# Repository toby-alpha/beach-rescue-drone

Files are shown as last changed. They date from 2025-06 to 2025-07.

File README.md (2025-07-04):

# Beach Rescue Drone & Dock





I designed (and will produce) a 7" drone capable of carrying a moderate payload that is a concept for a solution that would  assist in crucial life saving operations.

### Why did I design this?
 
Well... a drone is pretty cool, and my interests as soon as a saw this program definitely came to that straight away. Yet, I wanted to do something more meaningful than just a racing drone, something that could develop as unique, in a needing area. This really sparked my passion, and I feel like I was able to learn alot, while allowing my skills to thrive.

### What next?

Once all the parts arrive, there will be alot of assembly, and wiring to do. I'll be working off the Ardupilot firmware, so when I'm able to, I'll start adding that to the GitHub as well.

I'd love to answer any questions you have about this!

The STEP file contains all the CAD, it is uploaded in a ZIP file. Let me know if there are any errors with the conversions.

### PCB



### Wiring Diagram

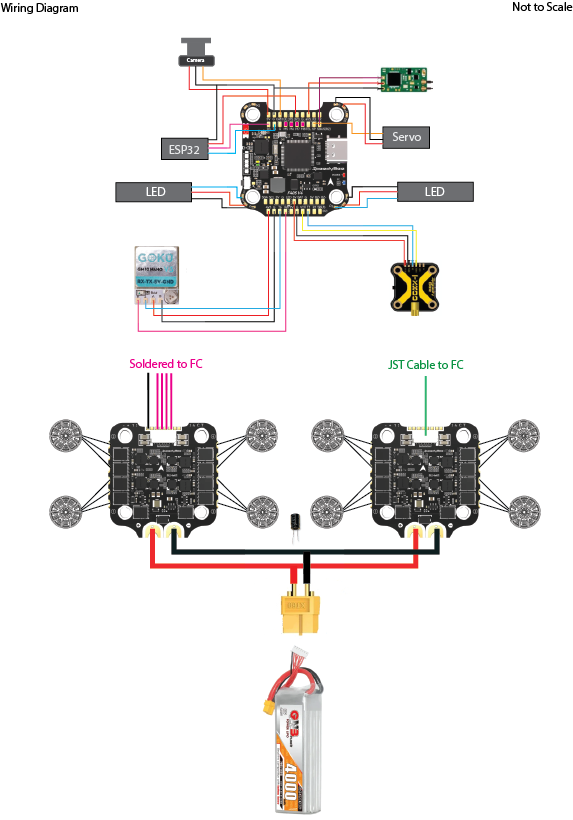
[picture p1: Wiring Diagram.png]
Wiring Diagram.png


### BOM

|Item |Cost (AUD)|Cost (USD)|Source |Link |
|---|---|---|---|---|
|2207 Motors x4 |0 |0 |Owned |N/A |
|Speedybee F405 FC |0 |0 |Owned |N/A |
|Speedybee 55A ESC |0 |0 |Owned |N/A |
|Reciever Module |0 |0 |Owned |N/A |
| | | | | |
|Speedybee 55A ESC |60 |39 |Aliexpress| |
|2207 Motors x4 |57 |37.05 |Aliexpress|https://vi.aliexpress.com/item/1005006356256645.html |
|VTX |40 |26 |Aliexpress|https://vi.aliexpress.com/item/1005006776832075.html |
|FPV Camera |38 |24.7 |Aliexpress|https://vi.aliexpress.com/item/1005009066346111.html |
|Servo and Parts |40 |26 |Aliexpress|https://vi.aliexpress.com/item/1005008716284050.html |
|ESP32 C3 |12 |7.8 |Aliexpress|https://vi.aliexpress.com/item/1005008813495235.html |
|7" Props |8 |5.2 |Aliexpress|https://vi.aliexpress.com/item/1005008250427353.html |
|Misc (bolts, standoffs)|25 |16.25 |Aliexpress|Misc. |
| | | | | |
|Aluminium Arms |150 |97.5 |Alibaba |PDF Quote (Provide upon individual request) |
|Carbon Fibre |120 |78 |Alibaba |PDF Quote (Provide upon individual request) |
|Middle Block |78 |50.7 |Alibaba |PDF Quote (Provide upon individual request) |
|Transmitter PCB |5 |3.25 |JLCPCB |PDF Quote (Provide upon individual request) |
| | | | | |
|Battery |119 |77.35 |PhaserFPV |https://phaserfpv.com.au/collections/6s-batteries/products/gaoneng-gnb-lihv-6s-228v-4000mah-70c-lipo-battery-xt60-dg|
| | | | | 
|Total |752 |488.8 | | |

## Part 2 



### Wiring Diagram


### BOM

|Item |Cost (AUD)|Cost (USD) |Source |Link |
|---|---|---|---|---|
|White PETG (14kg) |238 |154 |Siddament |https://siddament.com.au/products/white-petg-1-75mm-1kg |
|Black PETG (3kg) |48 |31.2 |Siddament |https://siddament.com.au/products/black-tpu-1-75mm-1kg |
|Linear Actuators x2 |160 |104 |Aliexpress |https://vi.aliexpress.com/item/1005006477151440.html |
|Breaker |9 |5.85 |Aliexpress |thttps://vi.aliexpress.com/item/1005006273365319.html |
|Control Board |7 |4.55 |Aliexpress |https://vi.aliexpress.com/item/1005004227086403.html |
|Control Panel |11 |7.15 |Aliexpress |https://vi.aliexpress.com/item/1005004227086403.html |
|Battery |29 |18.85 |Jaycar |https://www.jaycar.com.au/12v-6-5ah-sla-battery/p/SB2485 |
|Bearings |20 |13 |Aliexpress |https://vi.aliexpress.com/item/1005006822613982.html |
|Misc Hardware |40 |26 |Misc (Aliexpress)| |
|Total |535 |347.75 | | |

This dock is the second part of this project, and aims to serve as a succinct housing to complete it, overall completing the design goal set out at the start of the project.

Filament costs are tentative, yet on the lower side. Each piece takes roughly 1kg, and there will be 9. This doesn't account of support, or failures.

### Why I designed this?

After seeing the sucsess I had with the drone, I really wanted to nail in on the concept that I had created. The drone was great, but it needed a place to be stored. Thus, I was inspired to come up with this elegant solution. This makes my prototype become 1 step closer to a viable product, that'd be able to serve in a life saving capacity.

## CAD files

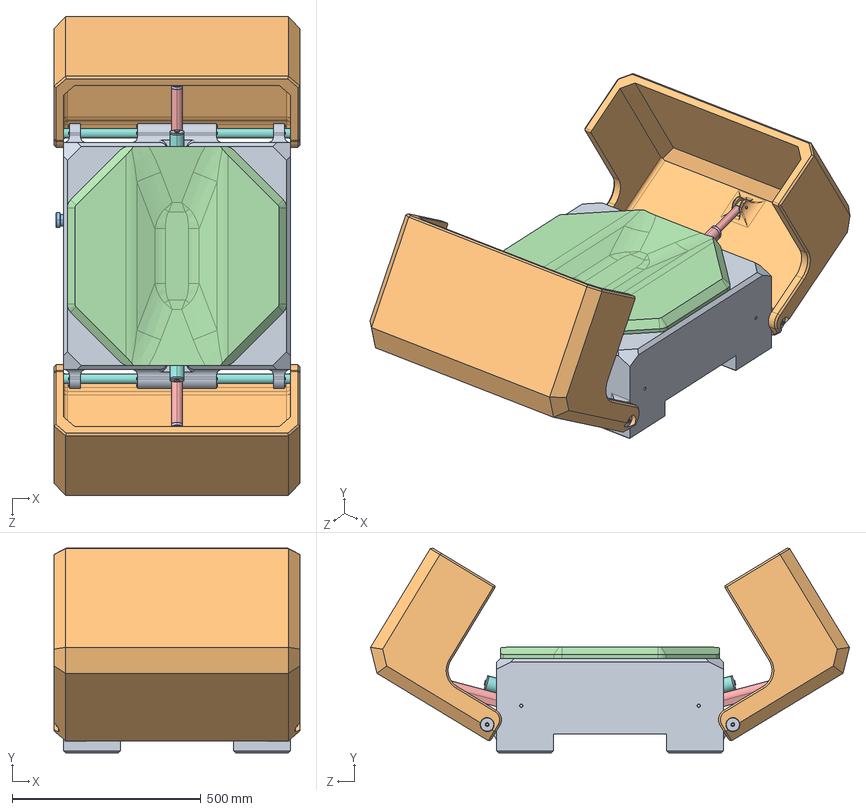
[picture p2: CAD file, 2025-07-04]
Part 2 - Dock/Dock Assembly.STEP
650.0 x 542.1 x 1267.4 mm
Base
Doors x 2
5972K281_Ball Bearing_5972K281 x 8
socket button head cap screw_am_B18.3.4M - 4 x 0.7 x 6 SBHCS --N x 32
25mm Tube x 2
Tube Stop x 4
m6 threaded rod x 2
M6 Lock nut.step x 4
Linear Actuator_Default<As Machined> x 2
Actuator Rod x 2
Door Cover
socket head cap screw_am_B18.3.1M - 5 x 0.8 x 12 Hex SHCS -- 12NHX x 4
Battery
Control Panel
Vector Ramp

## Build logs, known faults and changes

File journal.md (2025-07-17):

# Autonomous Beach Rescue Drone & Dock

### 36 Hours - Part 1 (Drone)
### 17 Hours - Part 2 (Dock)

## The Idea
Simply put: Create a prototype for an autonomous drone, that would be able to provide key first-aid rescue across Australia.

## The Current Situation
Australia's extensive coastline is both a national treasure and a significant public safety challenge. The coastline is understandably a popular location for recreation, being a gem of the world. Despite the efforts of Surf Life Saving (SLS) services, many areas remain unmonitored or difficult to patrol. During the 2024-2025 summer period (December to February), **51 coastal drowning deaths** were recorded.

Alarmingly:
- 65% of these drownings occurred more than 1 km away from a patrolled SLS service

- 40% were rip-related beach drownings, with

	-	27% of those involving bystanders attempting to rescue others.

- 60% occurred in regional or rural locations.

These statistics highlight a critical need for an initial rapid-response systems in unpatrolled and remote areas. Response in these areas is currently not feasible with traditional person-based approaches due to a lack of trained people available consistently, and a low amount of people on each beach.

To address this, there is an opportunity to develop an autonomous drone system which could be deployed as part of a system across **every Australian beach**. Especially targeting high-risk and unpatrolled zones.

## What Already Exists
Well.. not much.. really. 

Currently, there exists a solution which is deployed across the country, in which under human control, and deployment, drones are able to make rescues at major beaches. This has proven very effective. Yet, it still leaves a wide part of the country unprotected (60%), thus the need for an autonomous solution arises.

The current solution also allows for shark detection.

These Drones Are Saving Lives in Australia's Oceans | Hive Life Magazine

*Current drone in place at some major Australian beaches, at some times*

## Scope of the Project
**Design and Produce:**
- A mid sized drone (5-7"), based off the FPV framework.
	- The drone is capable of autonomous flight, to a pre-specified location, when directed.
- A solution to allow for the aerial drop of a commercially available inflatable floatation system
- A solution to allow the drone to be weather-proof and protected when not in flight.

**What will *NOT* be included in this scope, yet could be next :**
- Live Rescue tests
- Autonomous vision to detect people in need of assistance.
- Recharging while stored
*This was list was come to in order to ensure safety, and also make the project achievable in under 3 months*

### Time Spent - 2 Hours (27/05/25)

---

## Design - Start of the Dock
At beaches, conditions can become unpredictable, thus it is important to ensure that the drone will be able to be stored and protected during all weather conditions, especially where in rural areas in which regular interval maintenance is not feasible. However, this does not mean/make it realistic that this solution would be able to deploy in extreme weather conditions.

Naughty little girl threatens our summer fun | The Australian
*Extreme weather on Australian Beaches*

---
Thus, I think it'll be crucial to have a dock/station where the drone is able to rest, ready to deploy when needed.

**Requirements:**
- Weatherproof
- Facilitate accurate landing
- Cheap!
	- This drone has the ambition of being deployed in mass, thus price is an important factor.

**With this, some possible implementations:**
- Weatherproof
	- Closing lid
	- Storage drawer
- Facilitate accurate landing
	- Feedback to the drone
	- Use of AprilTags to help drone determine position

---
### What's Already on the Market

Something I firmly believe in is the analysis of existing products and solutions. This can often be overlooked.

Chances be it, most ideas have probably been explored and conceptualised in some form, thus having a good understanding of what has been done allows for an extra layer of innovation, in order to make a meaningful impact on the target market and consumers of the product.

---
**DJI Dock 1**
DJI Dock in Australia - FlytBase

> DJI's first generation of drone dock for autonomous deployment.

**✅ Advantages**
- Rugged and durable
- Lid swings open to provide a large landing area
- Secure - has security and sensors

**❌ Disadvantages**
- Expensive :)
- Landing accuracy relies on sensors in drone
	- Not practical for my application
- Requires an external power source to operate

---
 
**DJI Dock 2**
DJI DOCK 2 With DJI Matrice 3DT - Africa Drone Kings | DJI Drone

> Yeah.. so DJI is kinda popular. 

**✅ Advantages**
- Passive entering mechanism relies alot less on drone sensors to get it in
	- This is really cool
- Lid swings open using (by the looks of it) linear actuators, providing a simple, yet robust way of maximising the landing area, while using a very simple pivot mechanism.
**❌ Disadvantages**
- Expensive :)
- Landing accuracy relies on the drone - DJI has some pretty cool tech that allows this
	- Once again not feasible for my purposes.
- Requires an external power source to operate

---
**Energy Robotics Drone-in-a-box**
Image-Remove-Background

> AprilTags are pretty cool

**✅ Advantages**
- The April tags allow for very precise landings without requiring complex sensors
- Small (this is also a disadvantage)
- Sliding drawer improves safety during rain.

**❌ Disadvantages**
- Small. Could get covered over with debris is heavy weather
	- Landing pad size gives a big constraint.
- Seems like a less robust solution compared to DJI

---

**💡 Opportunities and What Worked Well**
- All solutions require an external power-source
	- Solar Charging to allow remote deployment
- The DJI passive centring is very neat, and a good solution to allow for reduced landing accuracy
- AprilTags seem like a good way to help the drone locate itself relative to the station.
- I think the fold out design appeal more at the moment, especially considering the terrain of the beach.

---
**Block CAD!!!**
Another thing which I see as really important is the use of Block CAD to help gain sense of key mechanism parts, and it really helps to plan a design solution. 

The goal here is to keep everything **as simple as possible**.

**Initial Concept - Heavily DJI Dock 2 Based**

I thought that the DJI Dock 2 provided a very succinct solution to the problem, and the concepts could provide very successful for my project.



The folding doors allow for a clear open space for the drone to take up out of, while then being able to fold in for a compact and succinct solution.

Additionally, the elevation of it allows for the potentially harsh conditions, and prevents it from getting covered and unable to open by sand or debris.



One thing I noticed from the DJI dock was how the indexing funnel was only on one side, and thus looked at implementing it I decided to experiment a bit with adding another flange on the other side. This would mean that there would be quite a large allowable margin for error when designing the landing system. This is a good thing!! It needs to work 100% of the time.



I feel like this concept has the ability to be pretty successful, and tomorrow I will look at trying something completely new involving sliding doors, just to get a sense of options.

I'm however cautious to design too much of the dock before the drone, as priorities will likely shift as the design of the drone (centre piece) evolves. It made sense to lay some groundwork for the dock first though.

**A final thought:**
Manufacturing.. oh yeah, this probably shouldn't be a final thought. Is anything on Day 2 a final thought though.. :)
I think it makes sense to try and utilise 3D printing as much as possible for this design, seeing as I'm aiming to keep the costs low for a small-quantity prototype. Industrial manufacturing process such as injection moulding don't make sense at small scale. 

Something interesting could be a aluminium frame on the inside to help with rigidity, this could be explored at a later time, once the design is more defined.

### Time Spent - 2 Hours (28/05/25)

---

## Day 2 - Further Dock Iterations 

The main goal for the dock mechanism is to be able to fold out in order to allow the drone to both take off, and land in a safe and accurate way, while also shielding it from the elements when not in use.

I identified another method of shutting the doors at the top, and rather than pivoting, have them side out of the way, like an opening hangar.



To accomplish this, I first took the base from the previous design, but the first thing I had to alter was the sides.

Seeing as the doors would be sliding out of the way, it would have to be fully enclosed from all sides. To do this, I raised all sides upto the same level.





I came up with something like this, using similar shaped doors as the previous model, but having them slide out of the way. Unfortunately, I don't think this option has much practical validity.



The doors could become quite heavy, which will come with the challenge of.. gravity. As the doors slide further out, the more force will be exerted on the mechanism that is holding it in place, to solve this, more overlap would be needed, yet this will reduce the amount of space the drone has to land in. I don't view this as an acceptable solution to the problem, harming the rigidity of the system.

Overall, I will not be pursing the sliding door archetype further, and will possibly look into some other solutions later down the track. Time to start the drone now!

### Time Spent - 2 Hours (30/05/25)

## Day 3 - Starting the Drone

I'll be designing a roughly 7" prop size drone, prioritising stability for autonomous flight operations.



I started off with a rough sketch of the dimensions, opting for a stretched X type configuration, to improve the speeds when travelling forward. This will be important when deploying for a rescue.

I currently have 2207 motors already, which have a 16mm mounting pattern, compared to the a more optimal motor for a 7" quad like the 2807, with a 19mm mounting pattern.



The arms will be manufactured from a 6mm carbon fibre sheet. I made the inner part thinner in order to reduce the thickness where not need around the motor mounts. The increased thickness is to prevent bending around the areas under a high load, and long lever. I'll run FEA analysis later to determine if more needs to be done to support this.





I'll also be using a coaxial 2207 setup. This gives a roughly 20% drop in efficiency, yet adds redundance, as if one of the motors breaks or stops during operation, the drone can keep flying. This is important for the high-stakes operating conditions that it'll be operating in. Currently, I have both motors stacked vertically ontop of each other, and am planning on doing a drilling one out to do a bolt through and tap into the other, yet I think this is likey to change.



This is a rough CAD mockup of one side, with the motors and 7" propellers. 



In the middle, there is a cutout which will be used to attach the arm mount to the main body.



and.... 7075 Aluminium Billet!! I played around (and still am) which this geometry to get it to be how I desire. This should allow for a rigid, but also strong frame that doesn't break under impacts, while allowing for easy mounting and attachment.

To allow the piece to become lighter, I'll be pocketing it once the geometry is more finalised. I'll likely have it produced at JLCCNC.



A general sketch of the drone layout, with the propellers raised, this allows for the payload to be safe from impacts from the downward facing motor. It was inspired by the DJI Inspire, but also other 8 motor Cinelifter type drones. Let's be honest, it looks pretty cool as well.





Something that I'm going to look into tomorrow is the pocketing of these arms, looking at the weight but also max deformation. I think the shape also needs a bit of work, the propellers seem too elevated at the moment.

### Time Spent - 1.5 Hours (31/05/25)

## Day 4 - Arm Optimisation

I started off by looking at mounting, and decided on using 4 counterbored M4 bolts per side. This offered a compromise between weight, and rigidity. The counterbore allows it to not get caught on anything.





These bolts will then go into tapped holes in the main body, providing a strong and secure connection



Now, the weight. Using 7075 over something like carbon fibre comes with many advantages in this application, but also disadvantages. One of the main ones is weight. Alot of this material in the middle isn't needed structurally, and can cut the weight in half. 

Most of these pockets were just done by sight, from previous experiences I've had.







Each motor gives of roughly 2000g of force (2kg), thus, applying 20N. To calculate the strength of this part, I'm assuming all 4 motors on each side are running at 100% (80N), plus 20N extra. This results in 100N of force being applied directly at the mounting point; however, this is probably unrealistic due to any slight flex in the carbon fibre arms.

Here are some of the test results.

No Skin


1mm skin


2mm skin


For each 1mm of skin, the deflection does down by roughly 0.1mm. I'll see how crucial this is later on in the project.

On a side note.. I'm not too sure of the accuracy of the simulation, but my research indicates anything less than 0.2mm deflection is optimal, so it's looking pretty good considering all of these are done under full load.

Just for fun, heres an example of the part not pocketed. Not too much of a difference which is pretty cool.


### Time Spent - 2 Hours (1/06/25)

## Day 5 - Bottom Plate

So I did a bit of a silly one... all the FEA was only done with one side of the arm. I'll be getting some quotes from machine shops in the coming days, but this has allowed me to consider whether I really need the full 25mm thickness.



I designed this small block to fit in the middle to allow both of the arms plates to be bolted together. This will currently be made of of 7075 billet as well, in order to ensure rigidity.



I then roughed up 2 plates which will serve as the main body. I don't really like how they look at the moment, and I find the shape to be a bit simple.



The plates were originally attached with 6 countersunk bolts each, but this is going to transition to being 4 to allow for a small bit of weight saving, while not compromising on rigidity.



I also added the RPI Zero 2 W, this will handle on-board april-tag recognition to allow for precise landing. This footprint is quite large on the drone.
 

The stack is mounted at the back of the drone, where the battery will sit ontop of. I have to use 2 of the 4-in-1 ESCs from Speedybee to accomodate the 8 motor setup.



I also designed a riser to allow for the ESP32 telemetry module to sit on. I'll be designing the PCB for this shortly. I'm not too happy with the layout at the moment. and I think I could 100% make it more efficient.

Tomorrow I'll be adding in the AprilTag camera, and maybe starting on the FPV camera as well. I had one idea to make that pivoting, but I'll see if it can be integrated into the budget, as currently it is looking very tight with the large expense of the CNC arms.

### Time Spent - 3 Hours (2/06/25)

## Day 6 - Further Refinements



As I mentioned yesterday, I wasn't too pleased with the overall shape. To improve the aesthetics I added a small taper at each end, which seemed to do it for me. I think just the overall boxy shape was what was weighing it down.



I mounted the AprilTag camera, I'll be using the OV9281-160. It's a monochrome camera, which will allow for faster processing on the Zero 2 W, and allow for a more responsive algorithm.



I also designed a mount for the FPV camera that the front that will be sending live video back to the operator.



I wanted it to be able to fit the VTX on the back due to size constraints, and this worked out pretty well. This will end up being 3D printed from TPU, or CF-Nylon.





I originally went with a smaller camera (10AUD), but ultimately realised this looked a bit out of proportion for my use and just looked a bit weird at the front. I also didn't like the fact that the PCB was exposed. I ultimatley went with a slightly more expensive option, but allowed for a much nicer solution. I felt like spending money here would be justified, and I'd prefer not having to order the more expensive option once I worked out the smaller one didn't work.





I also did this  case at the back that holds M4 standoffs,  for the carbon fibre plate, while also protecting all the electronics inside. I added a 3mm recess in the middle to allow for the ease of routing around the ESC, and I think this actually looks really good! This will probably be printed from CF-Nylon, and will add a nice stylistic touch on the side. 

It feels like it's definelty coming together now!

In other news, I've been contacting a few factories looking for machining services for the arm parts. These are very complex, and thus I'll need to outsource them. The company is doing this for a very reasonable price, with a low order quantity. These are made from 1" 7075 billet, which will definitely help with rigidity inside the drone. I would like to order 1 spare, unforchantly I don't believe I have space in the budget for this.

I'll be looking soon to finalise the part with wiring considered, then get it off to them for a final quotation.



I've also been in contact with a few for the carbon fibre as well, and there is one that looks very promising! Hopefully more on that tomorrow.

### Time Spent 3 Hours (4/06/25) 

## Day 7



I started today off by integrating an XT60 connector on the back. This will allow the battery to plug in, in a rigid way. I preferred this over having a loose pigtail due to it's reliability, with no additional cost. This also allows the inside to be completely protected. Yet, a problem I identified with this is potential build up of  heat inside. I'll look into how to fix this soon.





The camera has space inside for a small bit of pivot to allow for adjustments based on how I want it to look when flying. I don't really like aesthetically how it looks from the front.. but it's whatever. That can/will be changed later.



Wow! It look pretty good at this point. Here's a list of what I have left to go:

- Battery Mounting
- Drop Mechanism
- Antenna/GPS mounts.



and.. I found a problem. I only ever planned to have the carbon fibre arms supported from the top... whoops. I added a small recess to the bottom to allow it to be clamped down. 



My budget is looking pretty sad right now. Unfortunately I'm 180USD over. I already have some parts to construct this, but apparently it wasn't enough. I'll have to look how to cut a few cots, then I'm probably going to have to support it myself the rest of the way. My suppliers have all given very competitive prices, so I'll just have to see how things go and cut where possible.

### Time Spent 3 Hours (5/06/25) 

## Day 8 - Battery

I started today off by doing **alot** of reaserch on different battery options available to me locally, and eventually settled on this one.



I thought this offered a pretty good life-span, while delivering adequate power to the 8 motors. Unfortunately, it is a little bit pricy.. at 110AUD (70USD)



I designed this plate that would go on top to allow for the strap to rest underneath it, which is a pretty simple and succinct solution.

Tomorrow I'm going to look into doing the PCB for the telemetry, and then doing the antenna mount for that. The FlySky transmitter that I already have has an antenna built in, so I'll just need 2 mounts. 1 for the VTX and one for the Telemetry.

Just a short one for today.

### Time Spent 1 Hour (8/06/25)

## Day 9 - Telemetry Board

The cost has been worrying me for a while, so I decided to review the scope. I have ultimately chosen to not pursue the Pi with Camera for landing at the moment. This will come later in development, once the drone is proven to work, and I'll assess the need with how well the GPS works. This helps shave 80AUD (52USD) off the cost, which is helpful.

With that, I started work on the PCB for the telemetry. This will be pretty simple, using mounting holes and then solder pads breaking out the ESP32-C3. For the firmware, I'll be using the drone bridge firmware.





The PCB ended up being rather simple, with was unfortunate, but it'll do the job, and be functional for my needs.

### Time Spent 2 Hours (10/06/25)

## Day 10 - Finishing Touches



I added a hole for the USB-C port to allow access to the flight controller in the middle onto the side of the protective cover.



I also added a top facing GPS mount at the back. It is angled 10 degrees upward to assist with connection during inherently angled flight.



A hole then feeds into the back of the drone, allowing it to be connected to the main flight controller.



I also selected a servo and started cadding it. The main issue was finding one with a good enough drawing. Ultimatley, I did for a reasonable price, and also power. It'll fit perfectly (30mm in 30mm) inside the drone (once 2mm is filed off.. anyways). Tomorrow I'll integrate this into the billet block in the middle.

### Time Spent 2 Hours (12/06/25)

## Day 11 - Drop Mechanism



The manufactured ended up finding a step file of their product, and sent it to me overnight. This was really helpful in getting an accurate snapshot of the model.



The space which I have inside the middle block is... small at best. I think I struggled for like an hour on Aliexpress and Alibaba trying to find a compatible servo horn.. I was not successful. I'm going to just 3D print it and hope for the best, but it did help me build in the first of 3 stages for the linkage.



This one will hold a steel dowel pin, which will end up supporting the load.



This was Version 1 of the intermidate stage, which was later changed

Ultimatley, they all come together to be able to provide parallel and linear motion from the rotation of the servo.



The shaft will then be supported on 2 faces, such that it is always in contact with 1 bushing. This, as well as the vector 'funnel' in will be designed tomorrow.



Looks pretty nice. The packaging ended up working pretty well. I'm very pleased with how everything is going, and I want to be submitting by the end of the weekend so I can start ordering all the custom parts.

### Time Spent 4 Hours (13/06/25)

## Day 12 - Wiring Diagram

I have attached an image in the repo. This isn't final yet, but is unlikley to change. I designed it in Adobe Illustrator.

### Time Spent 1 Hour (14/06/25)

## Day 12.5 - Almost ready to ship.



As planned, I added a second bushing to serve as the linkage. In CAD this seems to work pretty well, but I suspect it will need some tweaks when all the parts arrive.



This is it in it's fully extended, compared to fully retracted states.



I also added 8 WS2812 LEDs on the front, to both serve as a flash for the camera, but to also provide a sense of direction to the drone. I think it kinda looks cools and changes the shape up a bit, adding visual interest.

I also changed the front plate shape to mirror this.





I also added 32 LEDs on the arm (16 each side) to provide enhanced visibility, enhancing safety. 





and that's the end product!! I think it looks pretty amazing.

As mentioned earlier (I think) I'll be using Ardupilot to program it, and thus can't do any work on the firmware until all the parts arrive.

Time to Ship!

### Time Spent 5 Hours (14/06/25)

## Day 13 - Ordering

With much success, I've pretty much ordered all my parts!

Slight problems were discovered. This motors which I originally planned on using were not sutiable, luckily, I was able to find 8 new ones on Taobao for a pretty similar price. I'll now be using 2810 1300KV motors.

### Time Spent 2 Hours (19-21/06/25)

## Day 14 - The Start of Part 2

I've split this project into 2 parts, the drone and dock, each bringing their own special challenges.

 Bridging from the block CAD at the start, I added some more detail to the pivoting doors.


The chamfer adds some visual depth, while then the holes at the bottom allow for the 25mm tube to fit through, which is then secured using compression.



This 25mm rod will then be supported by an array of bearings.



### Time Spent 3 Hours (2/07/25)

## Day 15
Today was fun, all the Aliexpress components have arrived! Everything looks in order. I'm just waiting on the factories producing custom parts to ship now, and it looks like assembly should start mid next week!!

Today, for the dock, I added in the linear actuators, which will provide the opening motion.

The linear actuators which I'll be purchasing have inbuilt stops, meaning it is possible to just apply 12V in 2 directions in order to achieve the full range of motion. This will end up heavily simplifying control.



This is it fully open.



This is it in the stowed state.



There is then a cutout in the main base to house the actuator.



In terms of control, it'll be powered off a 12V lead-acid battery. Then a custom control board will be made based off a SeedStudio Xiao (or similar based on how many pins I need) to interface with both this button panel, and a stack light to provide visual and auditory feedback.

The button panel will allow for manual operation during the prototype phase.



The stack light (which will be similar to the one below) also contains a buzzer, useful to help prevent accidents.


### Time Spent 4 Hours (3/07/25)

## Day 16

Today I was going to start with designing the PCB, though, I pretty quickly found the exact thing that I needed on Aliexpress. This will end up saving me time, allowing me to focus on other areas of development, and delivery heavy cost cuts.

This will also negate the use of a microcontroller, increasing reliability. Unfortunately, this also means I will not be pursing the stack light avenue.



With this, I added colour to the model. The white will be printed from PETG (I purchase this locally for 10USD per kg), and then the black landing pad from TPU, for extra wear resistance as the drone comes 'crashing' down into it (once again, 10USD per kg).





I also added the control buttons on, this will also serve as a door which can be opened to access the electronics inside.



Internally, there is also spacing of which the wires will run through.



With this, the design of the dock is done.

I finalised the readme, and have now submitted this second part of the project! Apologies if any of the images struggle to load.

### Time Spent 6 Hours (4/07/25)

## Drone Parts Update!

All components have arrived! The carbon fibre looks incredible. Yet, I'm currently messaging the CNC supplier, as they are having a slight problem with following their original timeline to ship the product.

A812F1EE-9033-4115-BD28-8F48BBA3D3E6_1_105_c

It's just anodising left, and hopefully it'll ship this week. Looking forward to starting to build this!!

### Time Spent 1 Horu (17/07/25)

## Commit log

2025-06-11 Initial bom
    [Export.csv]
2025-06-14 Added CAD
2025-06-14 Added PCB
2025-07-04 Add Part 2 Dock BOM
    [Dock BOM.csv]
2025-07-04 Added Part 2 Dock CAD
    [Dock Assembly.STEP]
